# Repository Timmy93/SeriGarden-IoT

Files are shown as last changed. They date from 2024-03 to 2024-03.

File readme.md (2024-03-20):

# SeriGarden

An IoT watering system that allow to water and monitor up to 4 plant per time. Server and Frontend can be set up inside your home and there is no need to communciate over internet (fully communicate over MQTT in the local network)

## Hardware requirements

### Main components

1x NodeMCU (tested Lolin v3) - Used to control plant
4x Water pump - Get water for plants
4x Capacitive Soil Moisture Sensor v2.0 - Measure soil humidity
1x Relay (4 ports) - Controls water pump
4x Inline Rectifier Diode (1N4007) - Used to control multilple sensor using 1 analog port

### Other suggestion

Stripboard to assemble components
Pin connectors to assemble easily components
Several meters of cable (26AWG - black, red and yellow in my case)
Several meters of heat-shrink tubing for a better cable management (2.4mm in my case)
1x Water box - A simple container filled with water. It's where water pump will be immersed

## Construction instruction

### Step 1 - Set up stripboard

- Solder the 4 diode (same pin for head, different for tail)
- Connect 4 pin for the 4 analog input
- Connect the 3 entry pin for analog, positive and negative

### Step 2 - Set up the the 4 humidity sensor

1. Cut 12 sensor wires *(4 red, 4 black, 4 yellow)* and 4 heat shrink tubes
2. Insert each group of 3 wires (rby) in a heat shrink tube
3. On one side, attach the female sensor connector to each group of wire
4. On the other side:

- Join the black cables together
- Attach the yellow cables to a female connector *(order is not important)* and isolate using small heat shirnking tube (insert **before** joining cables)
- Attach the red cables to a single female connector and isolate using small heat shirnking tube (insert **before** joining cables)

### Step 3 - Set up water pump

1. Cut 8 pump wires *(4 red, 4 black)* and 4 heat shrink tubes
2. Insert each group of 2 wires (rby) in a heat shrink tube and connect cables to the pump
3. Connect the black wires together to the board negative pole
4. Connect the red wires to each central port of relay (connect the 4° pump to the 3° relay due to known problems with nodemcu 1.0)
5. Connect wires from positive pole to the relay port on the left (pin of relay board are over the relay)

### How to assemble?

Pin D0, D1, D2 are used for the watering plant
Pin D5, D6, D7, D8 are used for monitoring plant

- Plant #1: connect pump to D0 and sensor to D5
- Plant #2: connect pump to D1 and sensor to D6
- Plant #3: connect pump to D2 and sensor to D7
- Plant #4: connect pump to D2 and sensor to D8

## Changelog:

v1.0 (30/07/2023): First release
Main feature

- Control 4 water pump and 4 humidity sensor using 1 NodeMCU (some problems with the 4° pump connected to D3)
- Receive watering control from server
- Communication over MQTT
- Plant ID is set up directly on MQTT

v2.0 (20/03/2024): Main design update

- Manage plant association directly from server
- Adding modular design to substitute failed components
- Known problem: the 4° pump is controlled together with the 3° due to a [problem](https://arduino.stackexchange.com/questions/95770/nodemcu-1-0-port-d3-relay-and-pump-does-not-boot) at boot

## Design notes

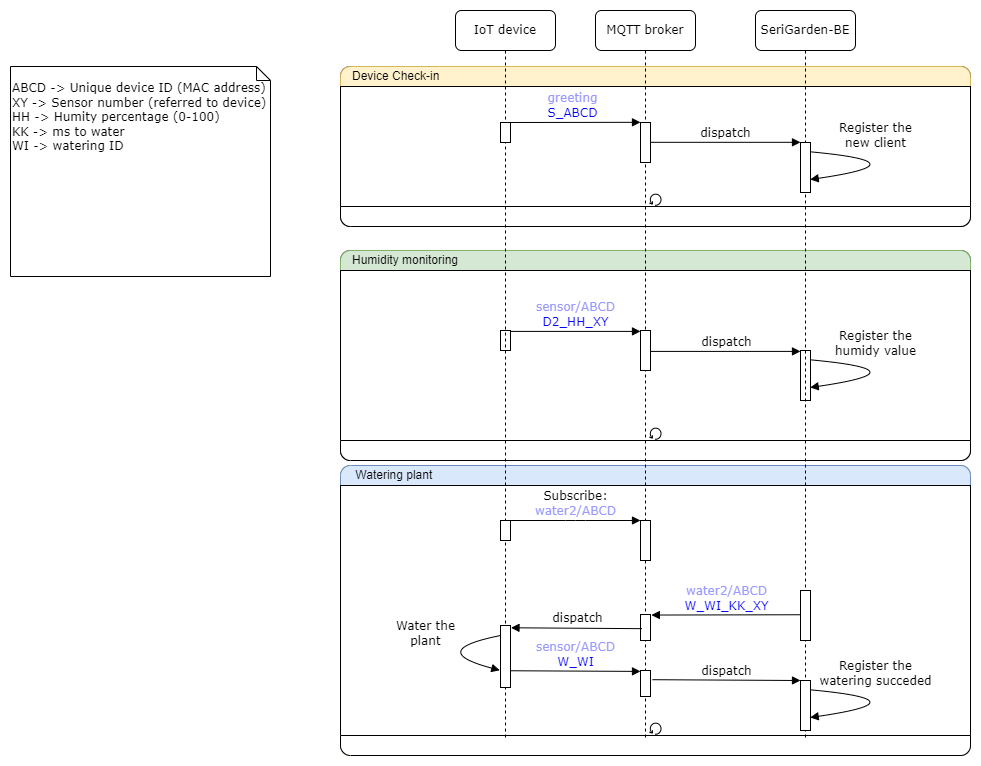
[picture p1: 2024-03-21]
Flowchart.png

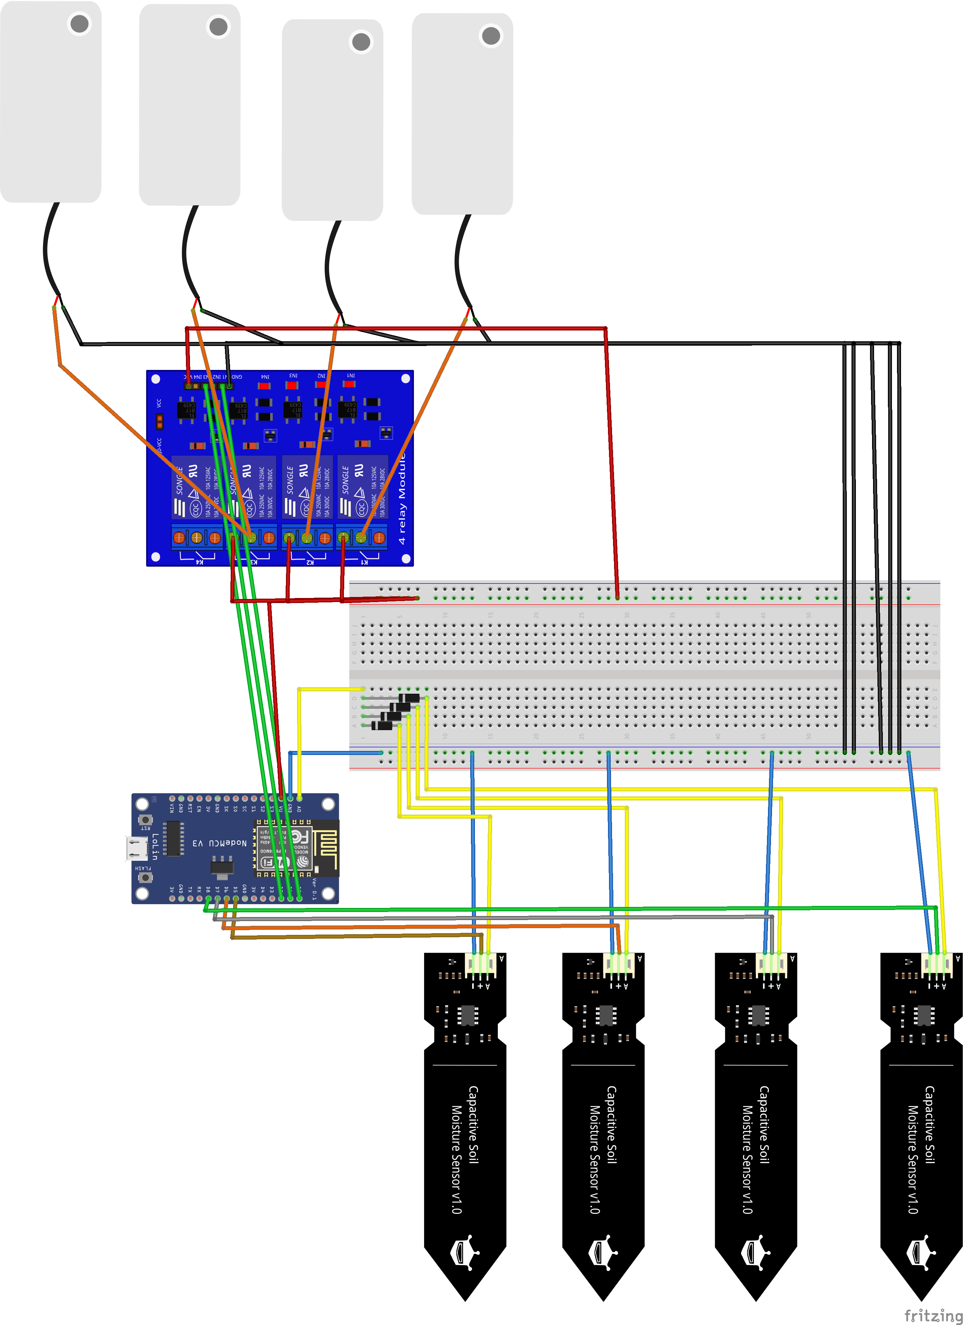
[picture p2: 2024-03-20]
schema_bb.png

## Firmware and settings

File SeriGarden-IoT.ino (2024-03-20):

#include <ESP8266WiFi.h>
#include <PubSubClient.h>
#include "secrets.h"
#define D0 16
#define D1 5
#define D2 4
#define D3 0
#define D4 2
#define D5 14
#define D6 12
#define D7 13
#define D8 15
#define A0 17
#define TX 1
#define RX 3

#define INNAFFIA 1000
// Minuti di attesa tra un'analisi e l'altra
#define LOOP_SLEEP 1
//Loop inattivi
#define NULL_LOOPS 60
#define WAIT 1000
#define MIN_HUM 550
#define MAX_HUM 190
#define MSG_BUFFER_SIZE	128

// Define the plants that are analysed
const int analyzed_plants[][2] = {
  // Non usare: D3, D4
  // OK: D0, D1, D2, D5, D6, D7, D8
  {D5, 1},
  {D6, 2},
  {D7, 3},
  {D8, 4}
};

//Define the plants that are 
const int watered_plants[][2] = {
  // Non usare: D4, D8, D3 (problemi avvio)
  // OK: D0, D1, D2, D5, D6, D7
   {D0, 1},
   {D1, 2},
   {D2, 3}
//   {D3, 4}
};

// Initialize clients
WiFiClient espClient;
PubSubClient client(espClient);
unsigned long lastMsg = 0;
char msg[MSG_BUFFER_SIZE];
int iteration = 0;
int ID = -1;
int first_run = 1;

void setup() {
  //Initial setup
  Serial.begin(9600);
  Serial.println("Inizializzazione... ");
  setupPin(true);
  //Get ID
  ID = ESP.getChipId();
  Serial.print("NodeMCU ID: ");
  Serial.println(ID);
  delay(3000);
  //setupPin(true);
  //Connect to WiFi, MQTT server and subscribe to MQTT topic
  setup_wifi();
  client.setServer(MQTT_SERVER, MQTT_PORT);
  client.setCallback(callback);
  Serial.println("Connettività configurata");
  
}

void setupPin(bool bootTime) {
  //Setup all plant to anlyse
  int len = sizeof(analyzed_plants) / sizeof(analyzed_plants[0]);
  int pin = -1;
  for (int i = 0; i < len; i++) {
    pin = analyzed_plants[i][0];
    if (bootTime) {
      pinMode(pin, OUTPUT);
    }
    initializeThisPin(pin, bootTime, LOW);
  }
  //Setup all plants to water
  len = sizeof(watered_plants) / sizeof(watered_plants[0]);
  for (int i = 0; i < len; i++) {
    pin = watered_plants[i][0];
    if (bootTime) {
      pinMode(pin, OUTPUT);
    }
    initializeThisPin(pin, bootTime, HIGH);
  }
}

void initializeThisPin(int pin, bool bootTime, int status){
  if (bootTime && (pin == D3 || pin == D4)) {
    //During boot this PIN must be HIGH
    digitalWrite(pin, HIGH);
  } else {
    digitalWrite(pin, status);
  }
}

// the loop function runs over and over again forever
void loop() {
  setupPin(false);
  int len = sizeof(analyzed_plants) / sizeof(analyzed_plants[0]);
  // Connect to WiFi and MQTT server
  if (!client.connected()) {
    reconnect();
  }
  client.loop();
  if (first_run == 1) {
    first_run = 0;
    // In fase di debug, fai un ciclo di irrigazione con tutte le pompe
    debug_pumps();
    greeting();
    Serial.println("Checking in...");
    delay(5000);
  }
  if (iteration % NULL_LOOPS == 0) {
    //Measure humidity for all the connected plants
    Serial.println("Start plant analysis... ");
    for (int i = 0; i < len; i++) {
      measure_hum(analyzed_plants[i]);
    }
    Serial.println("Plant analysis completed");
    iteration = 0;
  } else {
    Serial.print(".");
  }
  iteration += 1;
  delay(LOOP_SLEEP*1000);
}

void greeting() {
  String topic = "greeting";
  String payload = "s_";
  //TODO
  char topic_c[MSG_BUFFER_SIZE];
  char payload_c[MSG_BUFFER_SIZE];
  //Create output
  topic.toCharArray(topic_c, MSG_BUFFER_SIZE);
  payload = payload + ID;
  payload.toCharArray(payload_c, MSG_BUFFER_SIZE);
  //Publish message
  client.publish(topic_c, payload_c);
}

void measure_hum (const int plant_details[]) {
  //Define variables
  int pin = plant_details[0];
  int plant_id = plant_details[1];
  String topic = "sensor/";
  String payload = "d2_";
  char topic_c[MSG_BUFFER_SIZE];
  char payload_c[MSG_BUFFER_SIZE];
  //Read value
  int hum_v = read_pin(pin);
  //Create output
  topic = topic + ID;
  topic.toCharArray(topic_c, MSG_BUFFER_SIZE);
  payload = payload + hum_v + "_" + plant_id;
  payload.toCharArray(payload_c, MSG_BUFFER_SIZE);
  Serial.println(topic);
  Serial.println(payload_c);
  //Publish message
  client.publish(topic_c, payload_c);
}

int read_pin(int pin_to_read) {
  int value;
  float perc;
  String message = "";
  digitalWrite(pin_to_read, HIGH);
  delay(WAIT);
  value = analogRead(A0);
  delay(WAIT);
  digitalWrite(pin_to_read, LOW);
  perc = 100-((value-MAX_HUM)*100/(MIN_HUM-MAX_HUM));
  message = message + "Sensor: " + pin_to_read + " - Value: " + value + " - %: " + perc;
  Serial.println(message);
  return (int)perc;
}

void innaffiamo (int ilpin, int tempo){
//  int on = LOW;
//  int off = HIGH;
//  if (ilpin == D3) {
//    Serial.println("Special watering!");
//    on = HIGH;
//    off = LOW;
//  }
  int propagazione_acqua = 5000;
  if (DEBUG == 1) {
    propagazione_acqua = 500;
  }
  printf("Inizio ad innaffiare [pin: %d]\n", ilpin);
  digitalWrite(ilpin, LOW);   
  delay(tempo);              
  printf("Finisco di innaffiare, attendo la propagazione dell'acqua\n");
  digitalWrite(ilpin, HIGH);
  delay(propagazione_acqua);
}

// Connect to WiFi
void setup_wifi() {
  delay(10);
  // We start by connecting to a WiFi network
  Serial.println();
  Serial.print("Connecting to ");
  Serial.println(SECRET_SSID);

  WiFi.mode(WIFI_STA);
  WiFi.begin(SECRET_SSID, SECRET_PASS);

  while (WiFi.status() != WL_CONNECTED) {
    delay(500);
    Serial.print(".");
  }

  randomSeed(micros());

  Serial.println("");
  Serial.println("WiFi connected");
  Serial.println("IP address: ");
  Serial.println(WiFi.localIP());
}

void reconnect() {
  // Loop until we're reconnected
  while (!client.connected()) {
    Serial.print("Attempting MQTT connection...");
    // Create a random client ID
    String clientId = "ESP8266Client-";
    clientId += String(random(0xffff), HEX);
    // Attempt to connect
    if (client.connect(clientId.c_str())) {
      Serial.println("connected");
      subscribe_topic();
    } else {
      Serial.print("failed, rc=");
      Serial.print(client.state());
      Serial.println(" try again in 5 seconds");
      // Wait 5 seconds before retrying
      delay(5000);
    }
  }
}

void subscribe_topic() {
  Serial.println("Subscribing to topic");
  String topic = "";
  char topic_c[MSG_BUFFER_SIZE];
  //Create output
  topic = "water2/";
  topic = topic + ID;
  topic.toCharArray(topic_c, MSG_BUFFER_SIZE);
  Serial.print(topic);
  Serial.println(" - Sottoscritto!");
  client.subscribe(topic_c);
}

void callback(char* topic, byte* payload, unsigned int length) {
  Serial.println("MQTT message received");
  char* token_topic;
  char* token_payload;
  int water_id = -1;
  int ms = -1;
  int plant_id = -1;
  int required_sensor = -1;
  //Parse received payload
  char p_payload[length+1] = "";
  parsePayload(p_payload, payload, length);
  String message = "";
  message = message + "Message arrived [" + topic + "]["+p_payload+"]";
  Serial.println(message);
  
  //Extract info: 
  //  Parsing topic
  token_topic = strtok(topic, "water2/");
  required_sensor = atoi(token_topic);

  //  Parsing payload
  if (required_sensor == ID || 1) {
    // water2/12041068 - w_26_5439_2
    token_payload = strtok(p_payload, "_");
    token_payload = strtok(NULL, "_");
    water_id = atoi(token_payload);
    token_payload = strtok(NULL, "_");
    ms = atoi(token_payload);
    token_payload = strtok(NULL, "_");
    plant_id = atoi(token_payload);
    Serial.print("plant_num: ");
    Serial.println(plant_id);
    
    //Water the plant
    waterThisPlant(plant_id, ms, water_id);
  } else {
    Serial.print("Unexpected topic or sensor: ");
    Serial.println(required_sensor);
  }
  
}

// Convert the received message in a string
void parsePayload(char* parsed_s, byte* payload, unsigned int length) {
  for (int i = 0; i < length; i++) {
    parsed_s[i] = (char)payload[i];
  }
  parsed_s[length] = '\0';
}

void debug_pumps() {
  int pin;
  if (DEBUG == 1) {
  int len = sizeof(watered_plants) / sizeof(watered_plants[0]);
    for (int i = 0; i < len; i++) {
      pin = watered_plants[i][0];
      innaffiamo(pin, 3000);
    }
  }
}

/**
Executes the watering of this plant
*/
void waterThisPlant(int plant_id, int duration, int watering_id) {
  String message = "";
  message = message + "Plant ID: [" + plant_id + "] - Water ID: [" + watering_id + "] - Milliseconds [" + duration + "]";
  Serial.println(message);
  int pin = getPlantToWater(plant_id);
  if (pin > -1) {
    innaffiamo(pin, duration);
    sendWateringAck(plant_id, watering_id);
  } else {
    Serial.println("Ignoring request - Not handling this plant");
  }
}

int getPlantToWater(int plant_id) {
  int len = sizeof(watered_plants) / sizeof(watered_plants[0]);
  for (int i = 0; i < len; i++) {
    if (watered_plants[i][1] == plant_id) {
      return watered_plants[i][0];
    }
  }
  return -1;
}

// Acknoledge backend that watering was successfull
void sendWateringAck(int plant_id, int watering_id) {
  String topic = "sensor/";
  String payload = "w_";
  char topic_c[MSG_BUFFER_SIZE];
  char payload_c[MSG_BUFFER_SIZE];
  //Create output
  topic = topic + ID;
  topic.toCharArray(topic_c, MSG_BUFFER_SIZE);
  payload = payload + watering_id;
  payload.toCharArray(payload_c, MSG_BUFFER_SIZE);
  //Publish message
  client.publish(topic_c, payload_c);
}

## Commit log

2024-03-20 First release of SeriGarden-IoT
    [schema.fzz]
2024-03-21 Added flowchart
